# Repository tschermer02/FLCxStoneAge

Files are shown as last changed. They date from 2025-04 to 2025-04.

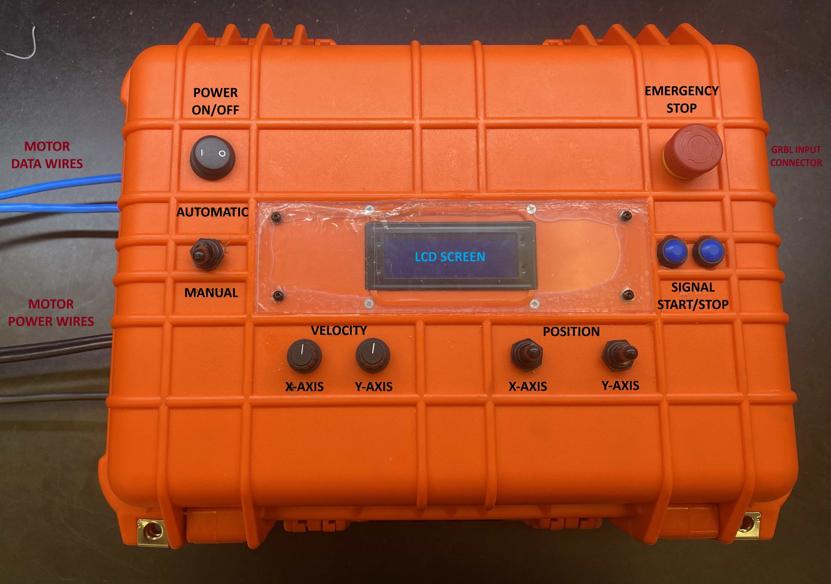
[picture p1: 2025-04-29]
guides/elecrtical_control_box_with_labels.jpg

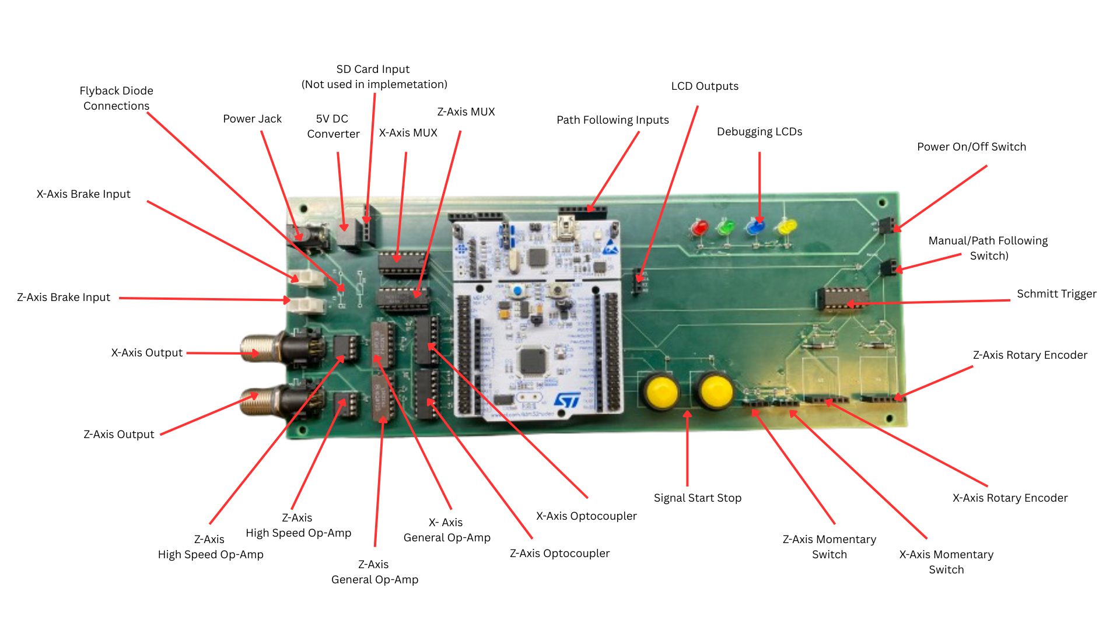
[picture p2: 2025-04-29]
guides/Labeled_PCB_layout.png

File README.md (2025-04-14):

# FLCxStoneAge Electrical Documentation

This repository contains all electrical schematics, layouts, firmware, and documentation for the StoneAge waterjet positioning system.

## Sections
- `schematics/`: Electrical schematics (PDF and source)
- `pcb/`: PCB layouts and design files
- `firmware/`: Manual and Path Following code for microcontrollers
- `components/`: Component lists and data sheets
- `installation_guides/`: Guides for assembling and wiring
- `safety_docs/`: E-Stop systems, power cutoffs, compliance notes

---

### 📥 Usage
Clone or download this repository to access the full documentation.

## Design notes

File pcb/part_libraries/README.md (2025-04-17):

This library is meant to contain the necessary part libraries that are required to develop the Control PCB.

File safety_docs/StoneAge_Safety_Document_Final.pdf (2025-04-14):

### StoneAge Electrical System Safety Document

WARNING: The system operates at voltages up to 75VDC. Use caution when working on live circuits.

This document outlines safety procedures and design considerations for the StoneAge dual-axis waterjet positioning system. It ensures that engineers and operators follow standardized practices for safe and efficient use of the system.

### 1. Purpose

This document outlines the key safety components, protocols, and procedures required for safe operation and maintenance of the StoneAge dual-axis waterjet control system. It is intended for engineers, technicians, and operators who interact with the electrical hardware.

### 2. System Overview

The electrical system powers and controls:
- A 2-axis motion platform
- ClearPath motors (NEMA 34)
- User interface box (UI box) with emergency stop and dual enable buttons
- Control logic (NUCLEO-F411RE MCU)
- Power conversion and safety interlocks

### 3. Safety Components

- Emergency Stop (E-Stop): Cuts motor power immediately and activates the dump valve
- Optocoupler Isolation: Prevents back current into logic systems
- Schmitt Trigger: Ensures clean digital signals to the microcontroller
- 5V DC Converter: Isolated power for logic
- Dual Motor Enable Buttons: Both must be pressed to activate motors; pressing either one disengages motor power

### 4. Startup Procedure

1. Supply power to the Teknic 75V power system
2. Then supply power to the 24V power system
3. Ensure E-Stop is disengaged (pulled out)
4. Press and hold both motor enable buttons to allow motion
5. Wait for motors to show idle/ready state

### StoneAge Electrical System Safety Document

### 5. Shutdown Procedure

1. Press either motor enable button again to disengage the motors
2. Turn off the 24V power system
3. Turn off the Teknic 75V power system
4. Press the E-Stop if full system lockout is required

### 6. Emergency Procedures

- If motion is unexpected or dangerous: Press E-Stop
- If smoke or smell: Shut off 75V and 24V power
- If software crash: Use manual disengage via enable buttons
- Water ingress: Shut off system, inspect and dry before reuse

### 7. Electrical Isolation Map

- 75V Power: Teknic motor supply
- 24V Power: Sensor and logic supply
- 5V Logic: Regulated and opto-isolated
- Dump Valve: Connected in series with E-Stop circuit

### 8. Maintenance Protocol

- Inspect the emergency stop and dump valve connection weekly
- Ensure both motor enable buttons are responsive and operate as intended
- Check all connectors for signs of corrosion or damage
- Only update or flash firmware when the system is fully powered down and locked out

### 9. Personal Protective Equipment (PPE) Guidelines

Wiring live circuits: Insulated gloves

### 10. Revision History

Version 1.0 - April 2025 - Initial draft created

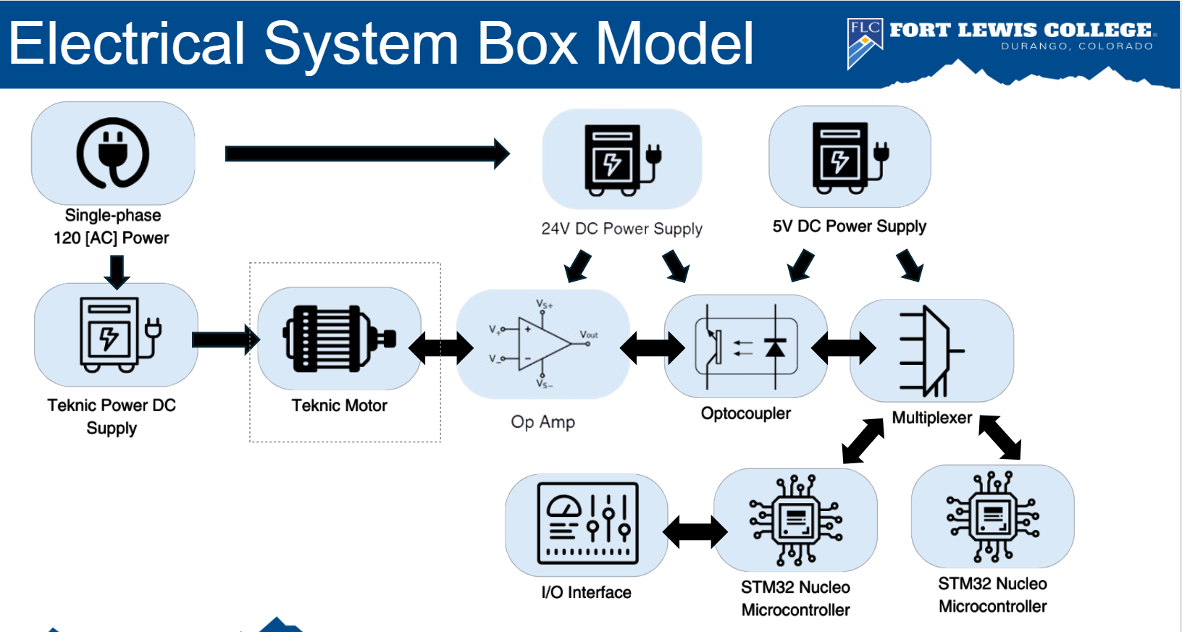
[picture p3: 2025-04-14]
schematics/FLC_box_model.png

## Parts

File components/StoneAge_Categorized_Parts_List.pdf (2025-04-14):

## Categorized StoneAge Parts List

This document contains clickable links grouped by category. Please confirm once the purchase has been

processed.

### Logic & Control Components

Optocoupler | Link (https://docs.broadcom.com/doc/AV01-0475EN)
Schmitt Trigger | Link (https://www.digikey.com/en/products/detail/texas-instruments/SN74HC14N/277223)
Multiplexer | Link (https://www.digikey.com/en/products/detail/rochester-electronics-llc/SN74LS157N/13528557)
NUCLEO-F411RE | Link (https://www.digikey.com/en/products/detail/stmicroelectronics/NUCLEO-F411RE/4866485)
Rotary Encoder | Link (https://www.digikey.com/en/products/detail/grayhill-inc/62A22-02-P/1834972)
USB-Infrared Communications Converter | Link (https://teknic.com/CPMS-USB-IR/)

### Interface & Display

LCD | Link (https://www.digikey.com/en/products/detail/sunfounder/CN0296D/18668625)
Push Buttons (Assorted) | Link (https://www.amazon.com/Waterproof-Momentary-Button-Switch-Colors/dp/B07F24Y1TB)
Toggle Switch Full Boot | Link (https://www.digikey.com/en/products/detail/bulgin/M1080-2/5058583)
On/Off Switch | Link (https://www.digikey.com/en/products/detail/bulgin/C3900BE/3462854)
Momentary Toggle Switch | Link (https://www.digikey.co.uk/en/products/detail/bulgin/C3922BA/5058166)
USB Mini B Panel Mount Extension | Link (https://www.amazon.com/RIKYJIC-Female-Network-Extension-Screws/dp/B0D8LH3HZY)

### Power & Conversion

5V DC Converter | Link (https://www.digikey.com/en/products/detail/traco-power/TSR-1-2450/9383780)
Diode | Link (https://www.digikey.com/en/products/detail/diodes-incorporated/SB140-T/21851583)
10 mF Capacitor | Link (https://www.mouser.com/ProductDetail/TDK/C1608X7T1A106M080AC)

### Passive Components

330-ohm Resistor | Link (https://www.mouser.com/ProductDetail/YAGEO/RC0402JR-7D330RL)
1K-ohm Resistor | Link (https://www.digikey.com/en/products/detail/yageo/RC0402FR-071KP/4935369)
2.2K-ohm Resistor | Link (https://www.mouser.com/ProductDetail/YAGEO/RC0402FR-102K2L)
10K-ohm Resistor | Link (https://www.digikey.com/en/products/detail/yageo/RC0402FR-1310KL/12082439)

### Mechanical & Enclosures

Apache 3800 Case | Link (https://www.harborfreight.com/3800-weatherproof-protective-case-large-orange-56766.html)

Break Wires | Link (https://www.homedepot.com/p/Syston-Cable-Technology-100-ft-22-2-White-CMP-Plenum-Rated-Fire-Security-Burglar-Station-Sound-Alarm-Control-Wire-UV-Resistant-Ind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)

### Connectors & Cables

Wurth Elektronik Barrel Jack | Link (https://www.digikey.com/en/products/detail/wrth-elektronik/694108106102/5047824)
8 Position Circular Connector | Link (https://www.digikey.com/en/products/detail/amphenol-ltw/M12A-08PMMR-SF7003/8637911)
8 Pin Panel Connector | Link (https://www.digikey.com/en/products/detail/te-connectivity-amp-connectors/T4171120008-001/9837148)
Two Pin Female Bulkhead Connector | Link (https://www.automationdirect.com/adc/shopping/catalog/cables_(terminated)/cable_connectors/zp-s1-2fr-0p3m)
Two Pin Male Bulkhead Connector | Link (https://www.automationdirect.com/adc/shopping/catalog/cables_(terminated)/cable_connectors/zp-s1-2mr-0p3m)

### Analog Components

High Speed Op-Amp | Link (https://www.ti.com/product/LM7171)
Operational Amplifier | Link (https://www.mouser.com/ProductDetail/Texas-Instruments/LM324J)

### Safety Components

Emergency Stop | Link (https://www.mouser.com/ProductDetail/IDEC/XA1E-BV304-R)

### Motors, Drivers & Accessories

NEMA 34 ClearPath-SDHP Model | Link (https://teknic.com/model-info/CPM-SDHP-3432H-ELS/?model_voltage=75)
Teknic IPC-3 Power Supply | Link (https://teknic.com/ipc-3/)
CPMS-CABLE-PWR-KK660 | Link (https://teknic.com/CPMS-CABLE-PWR-KK660/)
CPMS-CABLE-CTRL-AA660 | Link (https://teknic.com/cpms-cable-ctrl-aa660/)
POWER4-STRIP-S | Link (https://teknic.com/power4-strip-s/)
PC-SBR-72 | Link (https://teknic.com/pc-sbr-72/)
IPC35-CABLE110 | Link (https://teknic.com/ipc-3/)
Motor Power Cable (IP66K/IP67) | Link (https://teknic.com/CPMS-CABLE-PWR-KM120/)

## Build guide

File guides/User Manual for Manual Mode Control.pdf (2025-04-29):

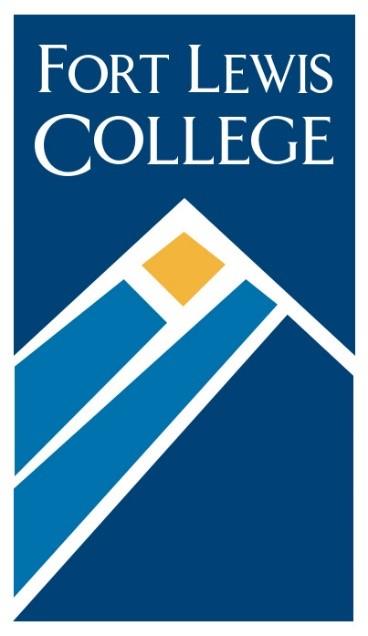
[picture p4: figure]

User Manual for Manual Mode Control Multi-Axis Positioning System for Water Blaster Testing Fort Lewis College Senor Design Team Spring 2025

Contents

1 - Summary of Manual Mode
Manual Mode is one of the two options available for controlling the testing rig made by the Fort Lewis College senior seminar team. This option is the faster and easier option, as no computer or path is needed to make the motors run. Only the buttons and switches on the electrical box are needed to move the testing rig. The downside to this mode is that the accuracy and consistency is lower due to being an open feedback system.
The manual mode also does not have any soft limit capabilities, meaning the system will not know the boundaries that the motors can move and relies on the torque sensors within the motor to stop them from crashing into the sides. This means extra precaution is required when working near the limits of the mechanical system.

2 – Controlling the Testing Rig
This section details what the manual system can do and how to access and control the testing rig
2.1 - Buttons and Layout
On the electrical box there is 10 different components that allow the operator to change or control the testing rig. The name of each component is:

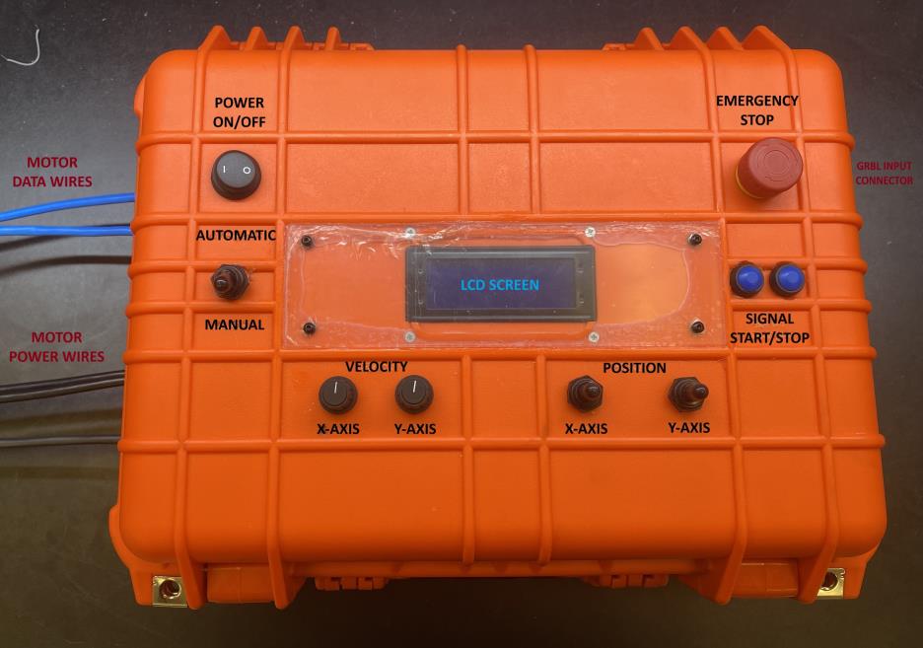
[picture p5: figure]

Fig 1: Top-down view of the electrical box showing the different components that the operator can use to control the system

Going from left to right top to bottom the following components are found:
Power switch:
This controls the power to the entire electrical box. flicking this switch on allows power to reach the microcontrollers within, allowing the ability for signals to be sent to the motors. LEDs:
The four colored LEDs are used to diagnose what state the manual system is in. More is discussed in the LED diagnostics section.
Emergency Stop:
When this button is pressed, all signals will cease, causing the motors to no longer be able to move. A signal to the dump valve is also sent. This signal must be set up during implementation to allow for the dump valve functionality to work.
Mode switch:
This switch controls which mode the system is in, either automatic or manual.
- LCD screen: Displays information and allows the operator to change settings when in manual mode.
- Motor enable buttons: Two buttons that work as a secondary on functionality to make sure the motors are enabled when wanted. More is discussed in the “Turning System on” section.
- X and Z rotary encoders: Controls multiple different functions with the rotational and press features these components bring.
- X and Z Momentary switches: When pushed and everything else is enabled correctly, these will move the motor in the corresponding direction.
2.2 - Turning the System on
To turn the manual mode system on, make sure the power is plugged in, and the power switch is turned on. Then set the mode switch to manual. If everything is working correctly, the LCD screen should display positional and velocity data of the motors.
To enable the motors so they can move you have to hold the rightmost motor enable button then to press the leftmost motor enable button. If done correctly, the yellow LED should be turned on, and the text on the info screen should be in all caps instead of camel cased. Pressing the leftmost motor enables button will disable the motors.

2.3 - Moving the Motors
Once the manual mode is turned on and is enabled, the motors can be moved. The speed shown on the LCD is the set max velocity of the motor. To change this, rotate the corresponding rotary encoder clockwise to increase the velocity or counterclockwise to decrease the velocity. The set velocity has a limit based on the motors. This value can be changed in the code if necessary.
Once the max set velocity is set, the motors can move by simply pushing the momentary switch in the direction the operator wants the motors to move. The X momentary can move left or right, so the operator can move the carriage left or right using the X momentary switch. The Z momentary switch can move up or down, so the operator can move the carriage up or down using the Z momentary switch.
2.4 - LED Diagnostice
Each LED is programmed to indicate a state that the manual system is in.
- Red LED: Emergency Stop is pressed; all operations have been cancelled
- Yellow LED: Motors are enabled and ready to be controlled
- Green LED: X axis is being sent signals to move
- Blue LED: Z axis is being sent signals to move
2.5 Changing Settings
Pressing either of the rotary encoders changes the LCD screen to display the options menu of that axis. To move around the options menu, the operator can rotate the rotary encoder clockwise to go down and counterclockwise to go up. Pressing the rotary encoder selects where the cursor is. The cursor is represented by a blinking line. Pressing the back symbol located at the top of any screen changes the LCD screen to display the previous screen. Moving the cursor onto either the downwards facing arrow or the upwards facing arrow will move the screen to show more settings.
Pressing the other rotary encoder switches the settings menu to the other axis. Rotating the other rotary encoder does nothing. With the options menu a few parameters can be changed to the fourth decimal. This includes the max set velocity and the velocity step (the amount the velocity changes when rotating the rotary encoder).
The linear regression model is the system used to roughly determine the velocity and position of the motor based on information from the operator. These values are defaulted to the values found by the senior seminar team. If you notice the velocities or positions being off, check the troubleshooting section to figure out how to calculate a new linear regression model.

Pressing the emergency stop or setting the system into automatic mode will cause the LCD to display if these features are turned on. Turning these features off will make the LCD screen be on the info screen.
3 – Accessing Code

All of the code and manuals will be provided on the GitHub the senior seminar team made. It is recommended to use the STM32 Cube IDE to upload any code to the STM32 microcontroller. The microcontroller can be programmed with a USB mini A adapter cable. Make sure everything is unpowered before uploading code. The IDE will not recognize the microcontroller unless the JP5 jumper is moved to jump the middle and right pin. This will set the microcontroller to be only powered by the USB. Once uploading is done, the JP5 jumper has to be switched back in order to be powered externally again. Below is a picture of the board with the JP5 jumper set to be powered externally by jumping the middle and left pin:

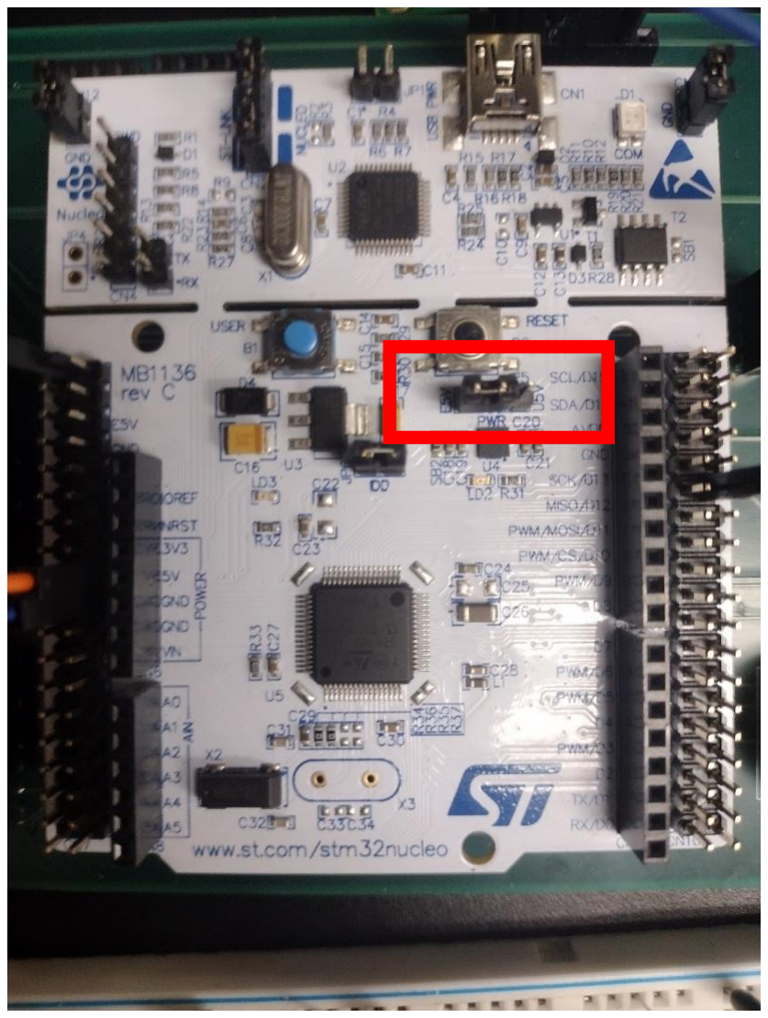
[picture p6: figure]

Fig 1: Top down view of the microcontroller. The JP5 jumper is highlighted and set to be powered externally instead of being powered via USB.

4 – Troubleshooting

4.1 - Calibration
The testing rig was calibrated before being implemented, but the system can go out of sync. If the gears were changed to a different size or the motors settings were changed using an IR sensor and ClearPath, the calibration will be off. This can be seen as the velocities not matching what the motors are outputting.
To calibrate an axis, the current linear regression for the axis must be known, and two runs of different velocities must be done. It is recommended to do one slow run (0.1-3 in/s) and one fast run (>3 in/s). the actual velocities of each run must be measured. The measured velocities should be as accurate as possible to allow the manual system to be as close as possible to what is being outputted. Once the current linear regression is known, the input velocities, and the measured velocities are found, inputting the variables into the following formula will give the calibrated linear regression:

Mcalibrated = Mcurrent

Vfast input − Vslow input

Vfast measured − Vslow measured

bcalibrated = Vslow input − Mcalibrated

Vslow measured − bcurrent

Mcurrent
Upload this calibrated linear regression to the STM32F411RET6 microcontroller that is directly on the green PCB and not the one within the 3D printed casing.
4.2 - Flickering
If the LCD is flickering or numbers are changing when they are not supposed to be, then there is an electrical disconnection causing an input to be floating. Check every electrical connection in the box that would interact with the LCD in the way that is flicking. If the velocity of an axis is flickering, check the momentary switch of that axis.
4.3 - Incorrect text in settings
Sometimes in the settings multiple rows get switched out with the same string or underscores. This happens when the rotary encoder is spun too fast, or the timers of the microcontroller happen to signal during a row transition. This bug is purely visual and will not affect the performance of the manual mode. If you need to read what was changed, simply move the rotary encoder until that row is selected. The row will display the correct string after it blinks.

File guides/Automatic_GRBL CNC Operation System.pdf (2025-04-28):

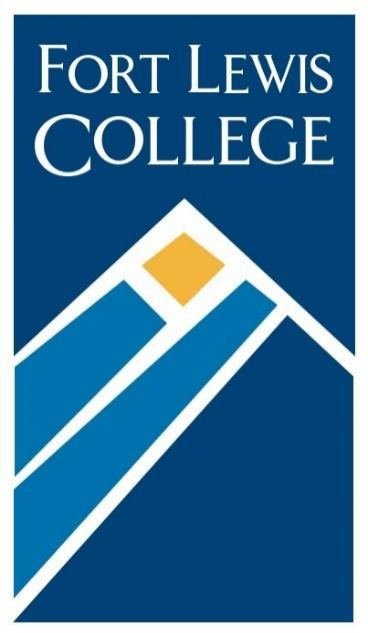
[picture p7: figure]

Automatic/GRBL CNC User Manual Multi-Axis Positioning System for Water Blaster Testing Fort Lewis College Senor Design Team Spring 2025

Contents

1 - System Overview
The automated system is driven by a Nucleo F411RE microcontroller running GRBL-Advanced, a fork of the open-source GRBL CNC firmware optimized for STM32 microcontrollers. This firmware interprets G-code commands and translates them into precise motion instructions for each axis of the system.
Motion is executed using Teknic ClearPath closed-loop servo motors, which integrate internal linear encoders that provide accurate feedback on motor position. These motors communicate motion status through the High-Level Feedback (HLFB) signal, enabling multiple safety interlocks within GRBL and precise movement tracking.
Through the graphical user interface (GUI), users can access core features such as homing, probing, toolhead/nozzle control, and spindle management. The GUI also supports manual jogging, macro execution, and real-time visualization of toolpaths. To generate G-code, many programs are supported, but only the most efficient programs for this machine are highlighted.
The key advantages of this control method include-Repeatable, consistent tool motion across successive tests.
Complex path execution for high-precision nozzle testing.
Scalable integration with nozzle/spindle controls.
Extensive safety features designed to prevent collisions before and during travel.

2 - Safety Information

- Always maintain a 15 ft buffer between operators and the nozzle per WJTA standards.
- Use the emergency stop switch to cut power and water instantly.
- Ensure water diverter valves and whip restraints are installed before running.
- Be sure all the wiring is clear from pinch points that may tear the harnesses.
- If travel moves are commanded outside the set axis limits, a soft limit will halt progress to prevent gantry collision.

- If soft limits fail to prevent collisions, the system will immediately stop when it hits a hard surface, preventing system damage.

2 – GSender/ LaserGRBL/Universal Gcode Sender GUI Features

2.1 - Startup
Double-check all power cords connected and plug a usb cable from a PC/Laptop into the type b connection exposed through the side of the electrical box. Bootup the preferred GUI and connect to board. Despite the multitude of GUI options available- GSender, LaserGRBL, and Universal Gcode Sender seem to offer the best balance of user-friendly controls with a powerful interface, suited for this application.
2.2 - Axis Mapping
To maintain compatibility with standard G-code generation programs, most of which assume a cartesian X-Y plane, the physical Z-axis of this system has been remapped to the logical Y-axis within GRBL firmware and the Nucleo pin configuration. This adjustment allows tools like Inkscape, JScut, and standard CAM software to generate toolpaths without requiring post-processing or reconfiguration. This allows users to interact with the system as if it were an X-Y machine with the intuition that actual motion occurs in the X-Z plane instead. As a result, when using a GUI like gSender, all Z-axis movements must be made using the Y-axis controls.
This remapping does not impact motion accuracy or system behavior, but it is essential to keep in mind that any “Y” axis inputs will be translated into “Z” coordinates while the established “Z” movements of any executed Gcode will be ignored.
2.3 - Jog Controls
- Use GUI arrows or keyboard to move in X/Z.
- Configure travel distances and move speed for each input.
- Hold shift for rapid movement.
2.4 - Gcode Execution
- Load .gcode file from local PC
- Preview and simulate toolpath
- Click “Run Job” to execute

2.5 - Macros
- Create reusable commands or save common test procedures here.
- To create a reusable macro without generating Gcode first- open a new console output, jog the axes at the preferred speed for the required travel distances, then copy/paste and save the Gcode output as a new macro once testing is completed. 2.6 - Console
Send commands such as-
- | $X | Unlock GRBL after reset or alarm state
- | $H | Home all axes using homing cycle
- | ?# | Show real-time machine status
- | ! | Pause the current job
- | ~ | Resume a paused program
Monitor Gcode outputs, travel motion, and any errors generated in real time.

3 – Gcode Generation Tools
Several G-code generation options are available, depending on application complexity and desired workflow automation.
The following tools are validated for use with the GRBL-Advanced firmware setup, supporting both simple and advanced motion patterns without the need for extensive post-processing.
3.1 - Inkscape + JScut for developing an SVG and processing into Gcode
Best for:
- Complex/Irregular line paths
- Circular motion patterns (supports G2/G3 command outputs)
- Execution of travel motion using existing 2D object files
Workflow:
1. Create drawing in Inkscape by uploading almost any 2D file or drawing the vectors directly.

2. Save as Plain SVG (important- no metadata).
3. Upload SVG into JScut (https://jscut.org) or download all Gcode extensions available for Inkscape on GitHub, allowing Gcode generation and path optimization within the GUI.
4. Configure tool settings (tool diameter, travel height, feedrate).
5. Generate GRBL-compatible G-code and download.
6. Load the .gcode file into GSender for preview and execution.
Notes:
- All CAM software used expects a traditional X-Y plane- the Gcode generated will move the Z-axis with Y-commands, and any Z-commands in the Gcode will be ignored.
- Set "Cut Depth per Pass" and "Final Depth" to zero, limiting unnecessary Z-commands in the generated Gcode.
- Inkscape can export Gcode directly to LaserGRBL, minimizing the number of steps throughout this process.
3.1 - Custom Python Gcode Generation and Logging
Scripts Used:
- GcodeGenerationandLogging.py
- Logging_Gcode.py
Best for:
- Complex mathematical motion paths (e.g., sinusoidal sweeps, parabolic curves)
- Simulates and logs dynamic acceleration, position, and feedrates.
- Generates visual outputs showing time vs position of each system axis. Workflow:
1. Modify motion parameters inside the CONFIG dictionary (start/end points, velocities, sample density, axis constraints, and type of path to take).
2. Run the script to generate:
- A .gcode toolpath file

- A .csv log file containing time-resolved kinematics
3. Review plots of velocity, position, and acceleration automatically generated by the script, double check no system constraints are being exceeded.
4. Load .gcode into GSender for execution.
Notes:
- Sampling resolution and feedrates must be configured based on the test goal (e.g., slow sweeps vs. rapid impulse).
- Built-in error handling prevents unrealistic acceleration or velocity violations, but especially in the case of the custom equation inputs for each axis, this script will throw errors if misconfigured, read all the docstrings before use.

4 – Motor Feedback Integration and Movement Tracking
HLFB (High-Level Feedback) Overview
Each Teknic ClearPath servo motor used in the system integrates an internal linear encoder that provides High-Level Feedback (HLFB) signals. These signals indicate motor status in real-time:

HLFB
State

Meaning

HIGH
(logic 1)

Motor is enabled and in-range (The system’s actual position is within an allowable range of steps compared to the commanded position)

LOW
(logic 0)

Motor is not enabled, has triggered an out-of-range error, or the system has hit a hard stop.

The HLFB output is wired to digital inputs on the Nucleo F411RE board, acting in place of physical limit switches. This configuration allows GRBL-Advanced to perform a homing procedure upon startup, moving the axes to set zero positions for the system, improving safety and repeatability. Any size object that will fit can be placed under the machine. During a homing or probing procedure, the nozzle will stop when it contacts that surface, setting the zero position accordingly. After the homing procedure is completed, the system relies on correctly calibrated parameters within GRBL firmware such as steps/mm and backlash compensation. When tuned precisely, the position and velocity of the system should be exactly as commanded by GRBL, making actual data collection an open loop process. It’s important these values are recalibrated whenever mechanical or MSP configurations occur, even when just installing different length box rails, as the axis limits must be changed accordingly as well, or soft limits disabled.
Important Notes:
- HLFB behavior is inverted compared to standard GRBL limit switch logic- firmware settings were adjusted to accommodate this.
- Soft limits, hard limits, and homing will be enabled. Soft limits prevent gantry collisions before they occur but can become annoying to change if the box rails of the system are consistently being swapped. In which case, disable soft limits and rely on the hard limits instead, which will shut down the motors when an unexpected hard stop occurs. Homing is required for repeatable testing.
5 - Key GRBL Parameters to Monitor and Adjust
Parameter Function | Typical Setting | Notes

$100,

$101 Steps per mm (X and Y logical axes) | Based on the set pulses/rev of the motor, gearing, and drive mechanics | Must be recalibrated whenever these factors change

$110,
$111

Maximum travel
speed (mm/min)

Limited by motor
performance and
safe load conditions

Tune conservatively for highpressure nozzle tests

$120,
$121

Acceleration
(mm/s²)

Defines axis speed
ramp-up and rampdown during travel
moves

Adjust to balance speed with mechanical stability

$130,
$131

Maximum travel
limits (mm)

Physical motion
limits for each axis

Critical to update after any mechanical length change,
subtract the carriage length from the new box rail

$140,
$141

Backlash
compensation

Based on measured
mechanical play

Enables improved positioning accuracy across direction reversals

Parameter Function | Typical Setting | Notes

distance (mm) for X
and Y axes
$20 | Soft limits enable
| 1 (enabled) or 0 (disabled) | Prevents software-commanded overtravel
$21 | Hard limits enable 1 (enabled)

Required for HLFB-based crash detection- turning this off won’t change motor behavior when encountering a hard stop, but the test will still appear to be running.

$22 Homing cycle enable 1 (enabled)

Must remain active for all test setups to ensure repeatability.

Notes
- There is no need to recompile firmware when making these changes, all settings are accessible within the mentioned GRBL-based Gcode senders.
- $140 (X) and $141 (Y) specify the measured mechanical backlash for each axis, defined as the distance the system must "take up the slack" after changing direction.
- These values are automatically compensated for during normal G-code execution, improving precision especially during oscillating movements, repeated reversals, or fine positioning tests.
- No additional speed control is associated with backlash compensation; the compensation moves are blended seamlessly into normal axis motion.

6 – Troubleshooting and Recovery
Even with properly configured systems, unexpected behavior or faults can occasionally occur. This section outlines common issues encountered during automatic operation and recommended steps for recovery.

Symptom | Possible Cause | Recovery Action
GSender will not connect to the board | USB cable not properly seated, board not powered, or incorrect COM port selected | Check all physical USB connections, power supplies, and select the correct COM port in the GUI- sometimes the wrong COM port will connect, but the GUI controls remain shaded. Try another COM port in this case.
Axis refuses to move after startup | GRBL is locked due to alarm state or emergency stop | Send $X unlock command via console and retry motion, this won’t work when homing is needed upon startup
Homing cycle fails or axis hits hard/soft limits prematurely | HLFB wiring fault, mechanical obstruction, or incorrect $130/$131 limits | Inspect wiring integrity, verify clear travel path, and confirm limit parameters are updated to current components
Soft limit alarm triggered immediately after homing | Logic is no longer inverted or the HLFB circuit has a fault | Check limit switch logic in GRBL firmware

Motor stalls or
vibrates without
moving

Step/Direction wiring
reversed

Verify correct Step/Direction/Enable wiring

Unexpected Gcode behavior
(ignoring Z-axis
moves)

G-code or jogging used Z-axis commands instead of
Y-axis

Regenerate G-code ensuring correct X-Y output orientation per axis mapping guidelines, don’t use the Z axis jogging controls

System freezes
during
operation

The green lights on the
motors turn orange due to
power or signal
fluctuation, can occur at
high commanded speeds
due to step pulse
frequency being too high

Reset system by pressing E-stop, reboot PC if necessary, and verify acceleration ($120/$121) and speed parameters are within motor capability. Lower the steps/rev of the motors using Clearpath MSP if the issue is noted at high speeds only. Check the 75v power supply is not overheating.

7 – Appendix
Firmware and Configuration Repository
All firmware used for the Nucleo F411RE GRBL-Advanced control system is based on the open-source repository-GRBL-Advanced GitHub Repository (https://github.com/Schildkroet/GRBL-Advanced)

In addition, all custom firmware specifically developed for this project, including manual mode control and path following operation, is available at:

FLCxStoneAge Project Firmware Repository (https://github.com/tschermer02/FLCxStoneAge/tree/main/firmware/pathfollowing)

This repository includes:

- Customized GRBL-Advanced source code tailored for the system hardware.
- Manual Mode firmware for direct operator control through buttons and LCD interface.
- Configuration files for motor steps, acceleration, and soft limit enforcement.
- System homing procedures, backlash compensation settings, and safety feature integrations.

Users seeking to modify or update the firmware should refer to the documentation provided within the repository for installation and configuration instructions.

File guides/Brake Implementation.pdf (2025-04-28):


### NEMA 23 Power-Off Brake Installation Guide

### Multi-Axis Positioning System for Water Blaster Testing

### Fort Lewis College Senor Design Team

### Spring 2025

### Contents

## 1 - Overview

Since the final design of the Multi-Axis Positioning System will not include the NEMA 23 Power-Off Brakes by the end of the Spring 2025 semester, this guide explains how to install and wire the brakes to the current hardware setup. Included along with this document is a PDF manual for the brakes, which contains installation and application details, dimensional drawings, and brake specifications.

For additional technical reference, visit the Teknic website: https://teknic.com/products/spring-applied-power-off-brakes/NEMA-23-brake/

## 2 - Mounting and Function

The NEMA 23 brakes are physically mounted, and keyed, between the motors and the gearboxes. Their main purpose is to limit motion along an axis when power is removed from the system.

Brake operates on 24V DC logic:

Logic HIGH (24V): Brake is released, allowing motion.

Logic LOW (0V): Brake is engaged, stopping motion.

To protect the circuit from inductive kickback or high-voltage spikes, a flyback diode is connected in parallel with each brake. This is included in PCB design.

## 3 – Wiring Instructions

The motor brakes each have two wires: one for power and one for ground.
These wires are routed from the brake assemblies into the user interface box, and then connected to the main PCB at header locations J3 and/or J6.

From the PCB, the brake power lines (B1 and/or B2) are routed through the emergency stop terminal block.
The circuit passes through the E-Stop, and then returns back to the corresponding B1 and/or B2 connections.

This wiring ensures that when the emergency stop button is pressed, electrical power to the brakes is immediately cut, causing the brakes to engage mechanically and stopping any further motion.

## 4 – Flyback Diode Placement

Flyback diodes are installed in parallel with the brake terminals. Place the diodes into the D1 and/or D8 pin locations on the PCB.

## 5 – Additional Notes

Ensure all connections match the system schematic before powering on. Use caution when handling inductive loads and verify proper diode orientation. The brake installation should be reviewed and tested during the commissioning phase to ensure proper system safety and response.

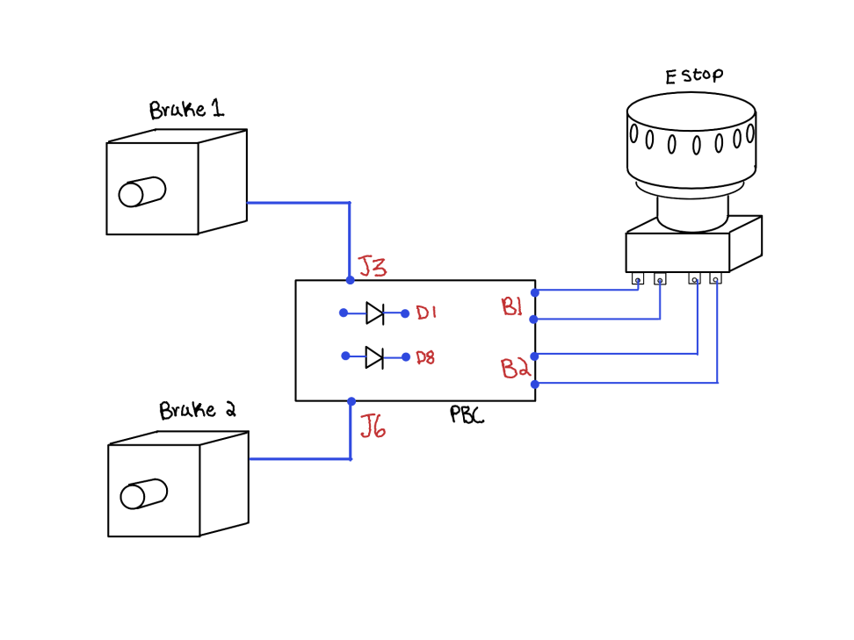
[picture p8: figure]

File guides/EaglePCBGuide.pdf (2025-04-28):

# How to Work with Provided Eagle PCB Files

## Download and Install Eagle

1. Visit the [Autodesk Eagle Download Page] (https://www.autodesk.com/products/eagle/free-download)
2. Create an Autodesk account if you don't already have one.
3. Download the installer compatible with your operating system (Windows, macOS, or Linux).
4. Install the application following the on-screen instructions.
5. Note: Eagle is now bundled with *Fusion 360 Electronics*, but you can still access Eagle independently.

## Open the Provided Files

1. Launch Eagle.
2. Navigate to File → Open → Project.
3. Locate the downloaded project folder containing the schematic and board files.
4. Open the .sch (schematic) file first to ensure netlists are correct.
5. Open the corresponding .brd (board) file to view the PCB layout.

## Add Any Missing Libraries

1. Identify missing libraries from Control Panel → Libraries → Used Libraries.
2. Download required .lbr files from trusted sources or request them from the project provider.
3. In Eagle:
a. Open Control Panel → Libraries.
b. Right-click and select Open Library Manager.
c. Under the Available tab, click Browse to add the .lbr files.
d. Enable the library by clicking the green checkmark.

## Review and Edit the PCB Layout

1. Verify that all components are placed properly.
2. Check routing and connectivity visually.
3. Use Tools → Ratsnest to ensure all nets are correctly updated.

## Run the Autorouter (if Necessary)

1. Select Tools → Autorouter.
2. Configure settings:
a. Layers (e.g., TOP and BOTTOM for two-layer boards).

b. Effort Level (start with "Medium").
4. Click Start to run the autorouter.

## Introduce or Verify Ground Planes

1. Select the Polygon tool from the toolbar.
2. Check if a GND polygon already exists.
3. If not, draw a rectangle surrounding the board outline.
4. Set the Signal Name to GND.
5. Click Ratsnest to fill the copper pour.

## Run Design Rule Check (DRC)

1. Go to Tools → DRC.
2. Load manufacturer-specific DRC settings if provided.
3. Click Check to run the analysis.
4. Fix any errors (and seriously review warnings).

## Export Gerber Files for Manufacturing

1. Open **File → CAM Processor**.
2. Use a predefined Gerber job (if available) or set up your own layer stack.
3. Export:
a. Copper layers (Top/Bottom)
b. Silkscreens
c. Solder masks
d. Drill files (NC Drill)
4. Package all exported Gerber files into a ZIP folder ready to send to a PCB manufacturer.

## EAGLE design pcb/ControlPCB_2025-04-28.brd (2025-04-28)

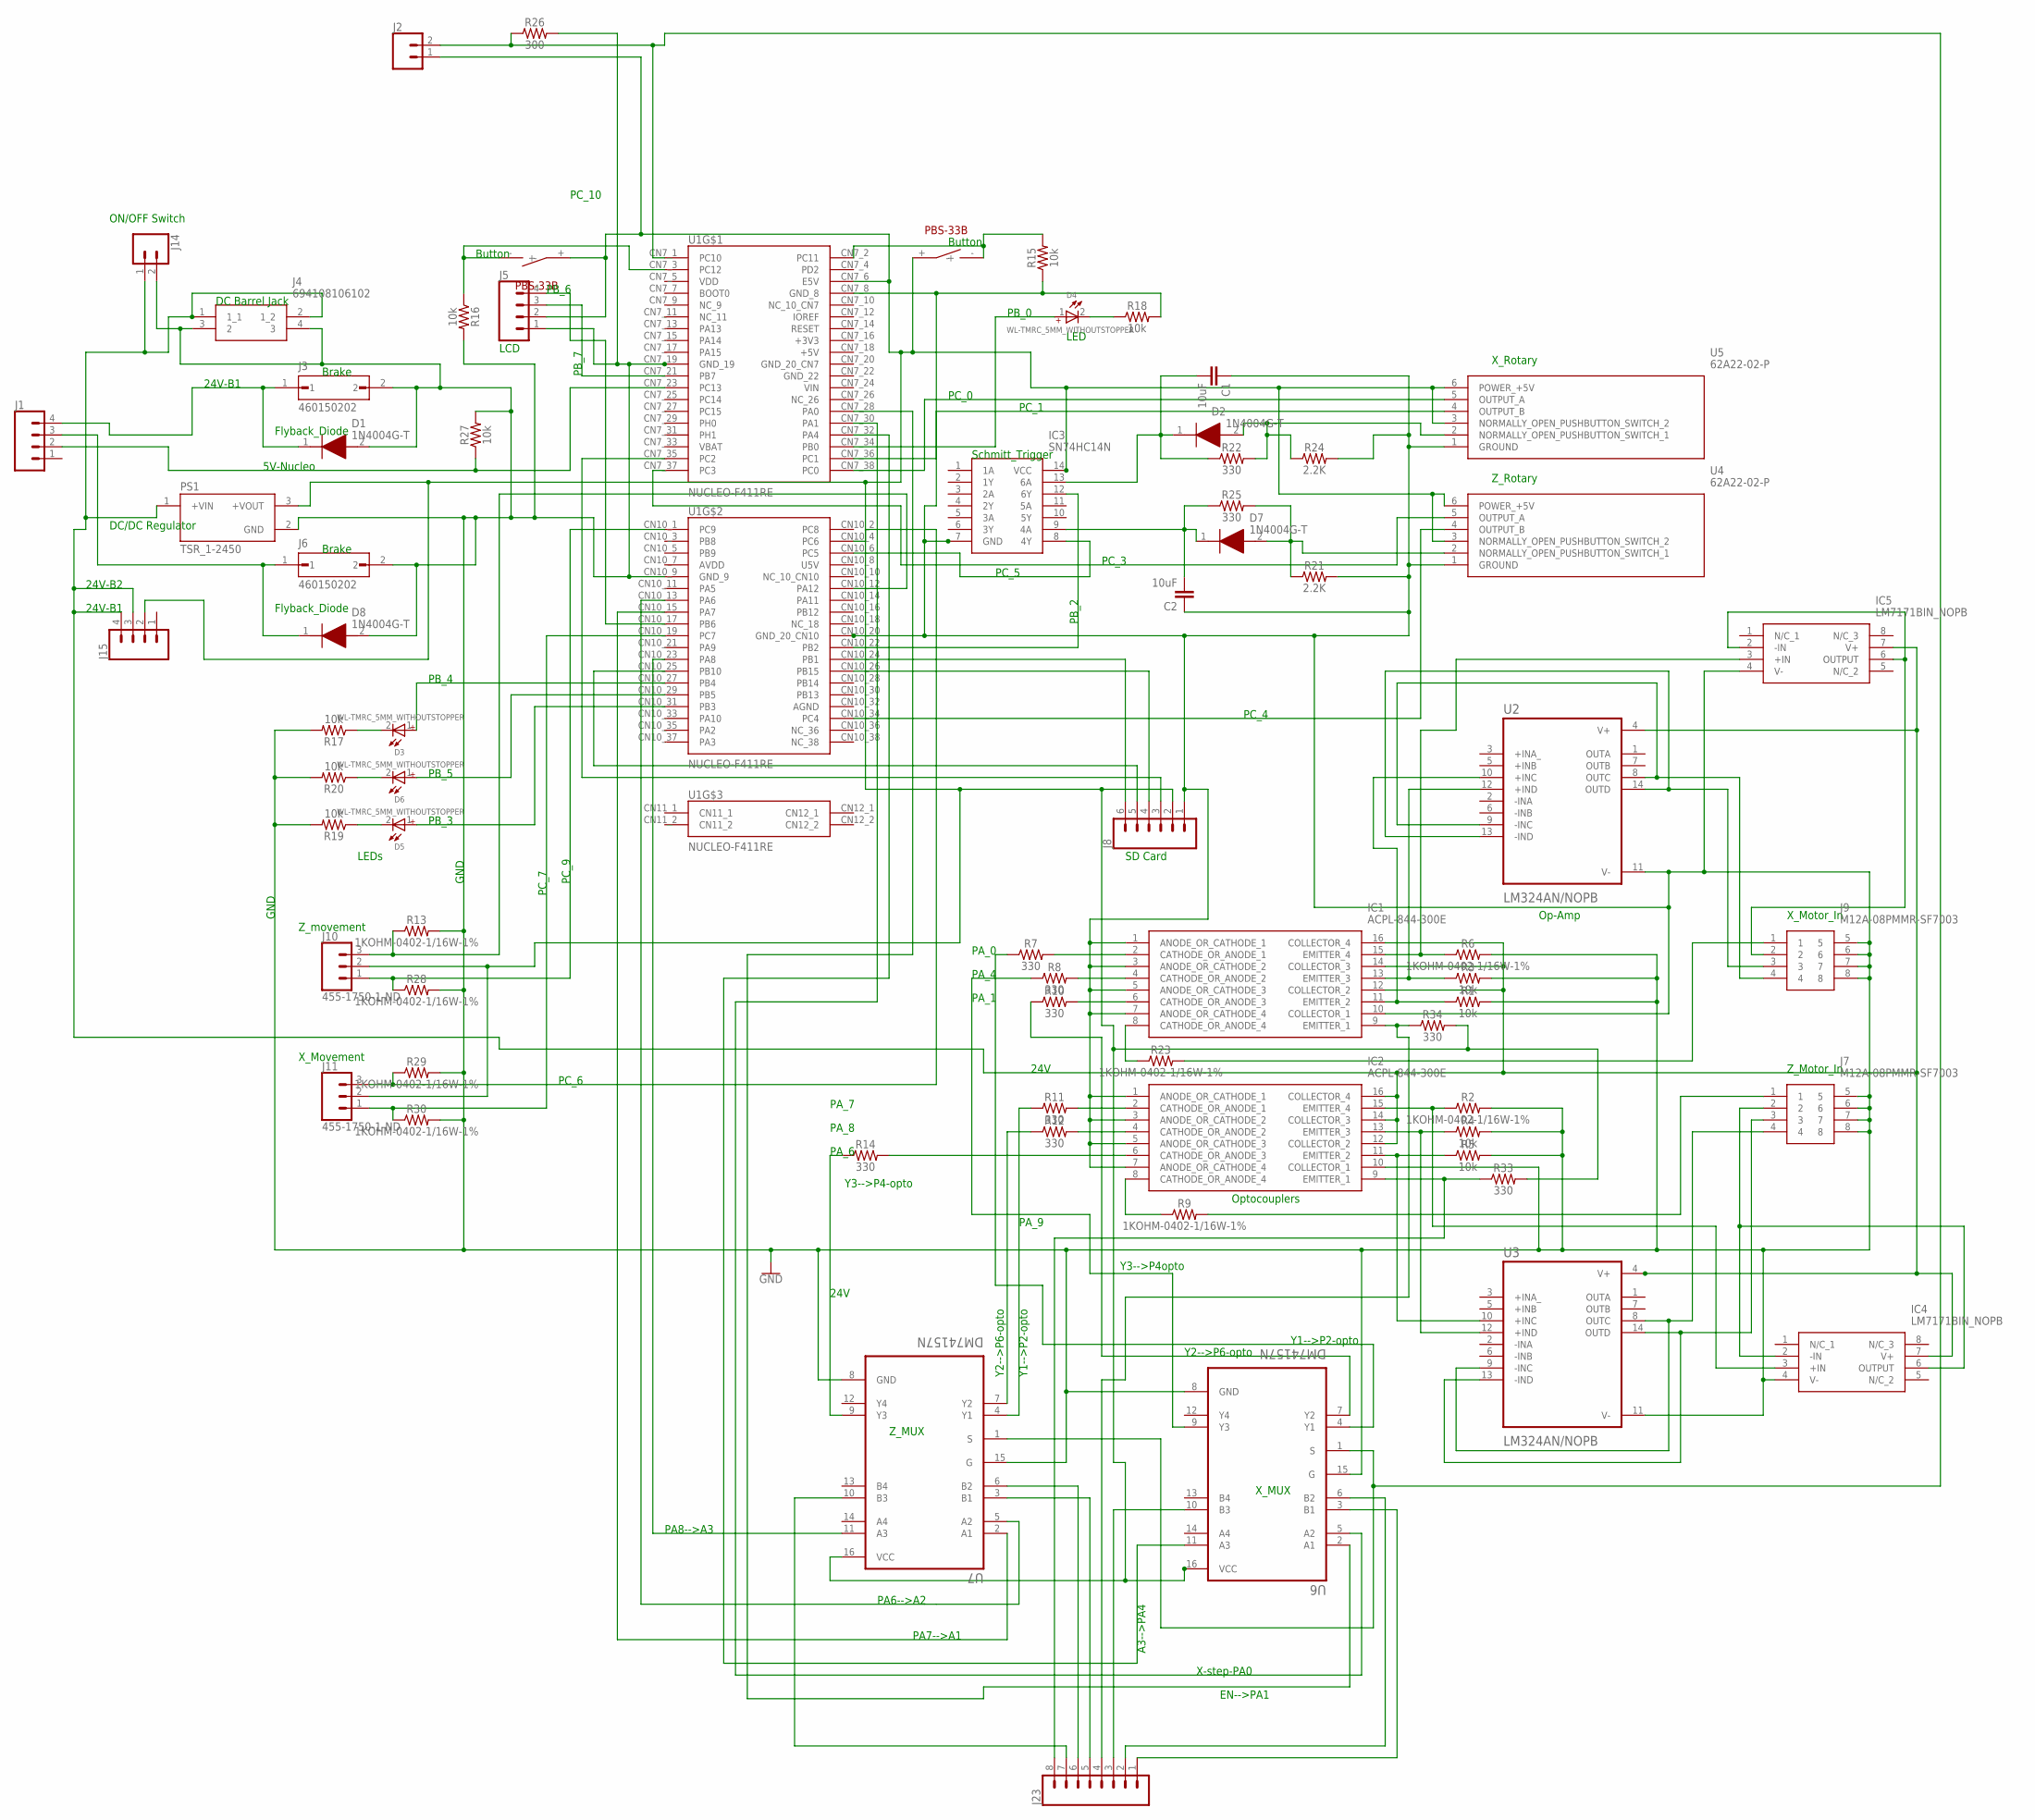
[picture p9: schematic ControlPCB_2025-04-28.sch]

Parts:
C1, C2: 10uF; 0603
D1, D2, D7, D8: 1N4004G-T; DIOAD1408W86L464D236
D3, D4, D5, D6: WL-TMRC_5MM_WITHOUTSTOPPER; WL-TMRC_5MM
IC1, IC2: ACPL-844-300E; DIP880W60P254L1984H450Q16N
IC3: SN74HC14N; DIP794W53P254L1930H508Q14N
IC4, IC5: LM7171BIN_NOPB; DIP794W53P254L959H508Q8N
J1, J15: CONN_04PTH; 1X04
J2, J14: CONN_02; 1X02
J3, J6: 460150202; MOLEX_460150202
J4: 694108106102
J5: CONN_04LOCK; 1X04_LOCK
J7, J9: M12A-08PMMR-SF7003; M12A08PMMRSF7003
J8: CONN_06SILK_FEMALE_PTH; 1X06
J10, J11: 455-1750-1-ND; 1X03
J23: CONN_08"; 1X08
PS1: TSR_1-2450; CONV_TSR_1-2450
R1, R3, R4, R5, R15, R16, R17, R18, R19, R20, R27: 10k; 0402
R2, R6, R9, R13, R23, R28, R29, R30: 1KOHM-0402-1/16W-1%; 0402
R7, R8, R10, R11, R12, R14, R22, R25, R33, R34: 330; 0402
R21, R24: 2.2K; 0402
R26: 300; 0603
U1: NUCLEO-F411RE; BOARD_NUCLEO-F411RE
U2, U3: LM324AN/NOPB; DIP794W45P254L1969H508Q14
U4, U5: 62A22-02-P; 62A2202P
U6, U7: DM74157N; DIP794W45P254L1918H533Q16
U$1, U$2: PBS-33B

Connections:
+3V3: U1.CN7_16 (+3V3)
+5V: U1.CN7_18 (+5V)
AGND: U1.CN10_32 (AGND)
AVDD: U1.CN10_7 (AVDD)
GND: C1.1, C2.1, D1.2 (A), D8.2 (A), IC1.1 (ANODE_OR_CATHODE_1), IC1.3 (ANODE_OR_CATHODE_2), IC1.5 (ANODE_OR_CATHODE_3), IC1.7 (ANODE_OR_CATHODE_4), IC1.10 (COLLECTOR_1), IC2.1 (ANODE_OR_CATHODE_1), IC2.3 (ANODE_OR_CATHODE_2), IC2.5 (ANODE_OR_CATHODE_3), IC2.7 (ANODE_OR_CATHODE_4), IC2.10 (COLLECTOR_1), IC3.7 (GND), IC4.4 (V-), IC5.4 (V-), J3.2, J4.3 (2), J4.4 (3), J5.1, J6.2, J7.5, J7.6, J7.7, J7.8, J8.1, J9.5, J9.6, J9.7, J9.8, J14.2, PS1.2 (GND), R1.2, R2.2, R3.2, R4.2, R5.2, R6.2, R13.2, R15.1, R16.2, R17.2, R18.2, R19.2, R20.2, R21.2, R24.2, R26.2, R27.2, R28.2, R29.2, R30.2, U1.CN7_8 (GND_8), U1.CN7_19 (GND_19), U1.CN10_9 (GND_9), U1.CN10_20 (GND_20_CN10), U2.11 (V-), U3.11 (V-), U4.1 (GROUND), U5.1 (GROUND), U6.8 (GND), U6.15 (G), U7.8 (GND), U7.15 (G)
GND_20_CN7: U1.CN7_20 (GND_20_CN7)
GND_22: U1.CN7_22 (GND_22)
unnamed: J10.1, R28.1, U1.CN10_1 (PC9)
unnamed: J9.4, U2.8 (OUTC), U2.9 (-INC)
unnamed: C2.2, D7.1 (K), IC3.9 (4A), R25.1
unnamed: IC2.9 (EMITTER_1), J23.8, R33.1
unnamed: IC2.2 (CATHODE_OR_ANODE_1), R11.2
unnamed: D8.1 (K), J1.3, J6.1
unnamed: J7.3, U3.13 (-IND), U3.14 (OUTD)
unnamed: IC2.8 (CATHODE_OR_ANODE_4), R9.1
unnamed: IC3.14 (VCC), J2.1, J5.2, J8.2, J10.2, J11.2, J15.2, PS1.3 (+VOUT), R33.2, R34.2, U1.CN7_6 (E5V), U4.3 (NORMALLY_OPEN_PUSHBUTTON_SWITCH_2), U4.6 (POWER_+5V), U5.3 (NORMALLY_OPEN_PUSHBUTTON_SWITCH_2), U5.6 (POWER_+5V), U6.16 (VCC), U7.16 (VCC), U$1.+, U$2.+
unnamed: J7.4, U3.8 (OUTC), U3.9 (-INC)
unnamed: D1.1 (K), J1.4, J3.1
unnamed: J7.1, R9.2
unnamed: IC1.4 (CATHODE_OR_ANODE_2), R8.2
unnamed: IC4.2 (-IN), IC4.6 (OUTPUT), J7.2
unnamed: R10.1, U6.7 (Y2)
unnamed: IC1.15 (EMITTER_4), IC5.3 (+IN), R6.1
unnamed: J23.7, U7.10 (B3)
unnamed: J23.6, U7.6 (B2)
unnamed: IC1.8 (CATHODE_OR_ANODE_4), R23.1
unnamed: IC5.2 (-IN), IC5.6 (OUTPUT), J9.2
unnamed: J23.5, U7.3 (B1)
unnamed: J1.2, R27.1, U1.CN7_23 (PC13)
unnamed: R16.1, U1.CN7_3 (PC12), U$2.-
unnamed: R15.2, U1.CN7_2 (PC11), U$1.-
unnamed: IC3.12 (6Y), U1.CN10_22 (PB2)
unnamed: U1.CN7_32 (PA4), U6.11 (A3)
unnamed: IC2.11 (EMITTER_2), R5.1, U3.10 (+INC)
unnamed: U1.CN7_37 (PC3), U4.5 (OUTPUT_A)
unnamed: R12.1, U7.7 (Y2)
unnamed: IC1.2 (CATHODE_OR_ANODE_1), R7.2
unnamed: IC1.12 (COLLECTOR_2), IC1.14 (COLLECTOR_3), IC1.16 (COLLECTOR_4), IC2.12 (COLLECTOR_2), IC2.14 (COLLECTOR_3), IC2.16 (COLLECTOR_4), IC4.7 (V+), IC5.7 (V+), J4.1 (1_1), J4.2 (1_2), J14.1, J15.3, J15.4, PS1.1 (+VIN), U2.4 (V+), U3.4 (V+)
unnamed: R7.1, U6.4 (Y1)
unnamed: IC1.6 (CATHODE_OR_ANODE_3), R10.2
unnamed: IC2.4 (CATHODE_OR_ANODE_2), R12.2
unnamed: U1.CN10_15 (PA7), U7.2 (A1)
unnamed: D7.2 (A), R21.1, R25.2, U4.2 (NORMALLY_OPEN_PUSHBUTTON_SWITCH_1)
unnamed: R11.1, U7.4 (Y1)
unnamed: U1.CN7_38 (PC0), U5.5 (OUTPUT_A)
unnamed: IC1.9 (EMITTER_1), J23.4, R34.1
unnamed: J9.3, U2.13 (-IND), U2.14 (OUTD)
unnamed: U1.CN10_34 (PC4), U4.4 (OUTPUT_B)
unnamed: C1.2, D2.1 (K), IC3.13 (6A), R22.1
unnamed: D4.1 (+), U1.CN7_34 (PB0)
unnamed: J5.4, U1.CN10_17 (PB6)
unnamed: D6.2 (-), R20.1
unnamed: D5.2 (-), R19.1
unnamed: D4.2 (-), R18.1
unnamed: D3.2 (-), R17.1
unnamed: J8.4, U1.CN10_26 (PB15)
unnamed: J8.5, U1.CN10_25 (PB10)
unnamed: R14.1, U7.9 (Y3)
unnamed: J9.1, R23.2
unnamed: U1.CN10_13 (PA6), U7.5 (A2)
unnamed: U1.CN7_30 (PA1), U6.5 (A2)
unnamed: U1.CN7_28 (PA0), U6.2 (A1)
unnamed: D3.1 (+), U1.CN10_27 (PB4)
unnamed: D6.1 (+), U1.CN10_29 (PB5)
unnamed: J5.3, U1.CN7_21 (PB7)
unnamed: J23.3, U6.10 (B3)
unnamed: J23.2, U6.6 (B2)
unnamed: D5.1 (+), U1.CN10_31 (PB3)
unnamed: U1.CN10_23 (PA8), U7.11 (A3)
unnamed: U1.CN7_36 (PC1), U5.4 (OUTPUT_B)
unnamed: J23.1, U6.3 (B1)
unnamed: D2.2 (A), R22.2, R24.1, U5.2 (NORMALLY_OPEN_PUSHBUTTON_SWITCH_1)
unnamed: J8.6, U1.CN10_24 (PB1)
unnamed: IC3.8 (4Y), U1.CN10_6 (PC5)
unnamed: J8.3, U1.CN7_35 (PC2)
unnamed: J2.2, R26.1, U1.CN7_1 (PC10), U6.1 (S), U7.1 (S)
unnamed: J10.3, R13.1, U1.CN10_12 (PA12)
unnamed: J11.3, R29.1, U1.CN10_4 (PC6)
unnamed: J11.1, R30.1, U1.CN10_19 (PC7)
unnamed: IC1.13 (EMITTER_3), R3.1, U2.12 (+IND)
unnamed: IC2.13 (EMITTER_3), R4.1, U3.12 (+IND)
unnamed: IC2.6 (CATHODE_OR_ANODE_3), R14.2
unnamed: R8.1, U6.9 (Y3)
unnamed: IC1.11 (EMITTER_2), R1.1, U2.10 (+INC)
unnamed: IC2.15 (EMITTER_4), IC4.3 (+IN), R2.1
U5V: U1.CN10_8 (U5V)
VBAT: U1.CN7_33 (VBAT)
VDD: U1.CN7_5 (VDD)

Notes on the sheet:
X-step-PA0
EN-->PA1
Y2-->P6-opto
A3-->PA4
Y3-->P4opto
Y1-->P2-opto
Y3-->P4-opto
ON/OFF Switch
DC Barrel Jack
Brake
Flyback_Diode
DC/DC Regulator
LEDs
X_Movement
Z_movement
SD Card
Optocouplers
Op-Amp
X_Motor_In
Z_Motor_In
Schmitt_Trigger
X_Rotary
Z_Rotary
X_MUX
Z_MUX
LED
Button
LCD
PC_9
GND
PC_6
PC_7
24V
PC_0
PC_1
PB_0
PA_0
PA_1
PA_4
PA_8

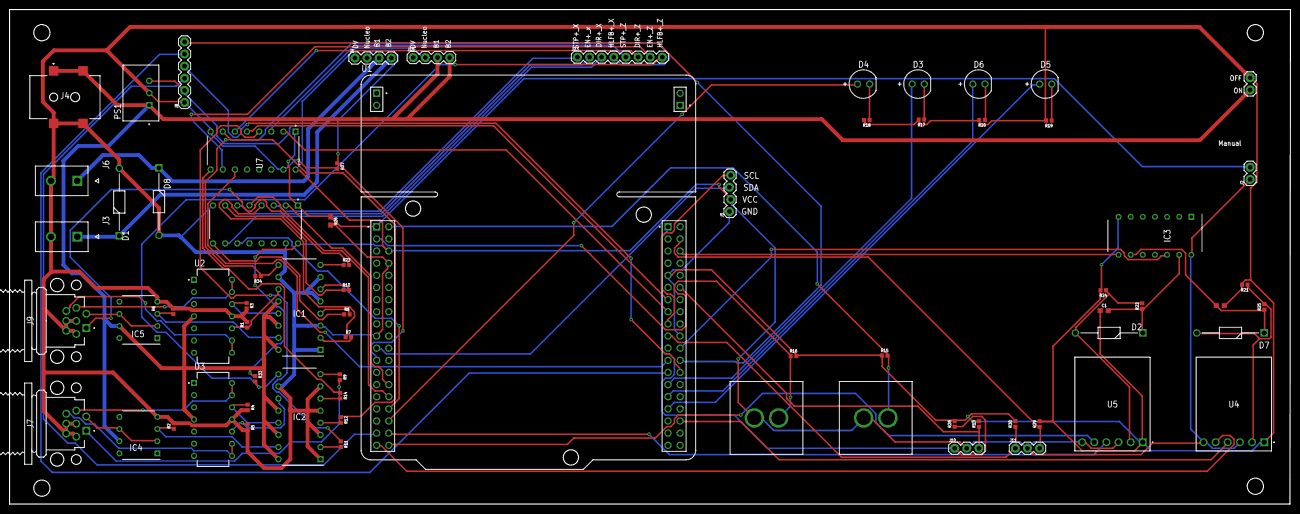
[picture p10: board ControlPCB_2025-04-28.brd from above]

Board: 4 copper layers, 268.0 x 103.5 mm, 71 parts (0 on the bottom side), 79 nets.

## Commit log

2025-01-16 Blinking LED Test
2025-04-28 Add zipped UGS and STM32CubeProgrammer installers with Git LFS
2025-04-28 Add zipped GSender and GRBL-Advanced software with Git LFS

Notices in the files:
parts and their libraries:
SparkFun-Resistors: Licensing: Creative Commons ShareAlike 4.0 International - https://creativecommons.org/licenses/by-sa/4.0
